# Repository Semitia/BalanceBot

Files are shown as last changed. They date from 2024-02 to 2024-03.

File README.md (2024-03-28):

## CAN负载率计算

考虑各类消息的发送端

| 单元 | FOC控制板 | TOF  | ICM  | RDK-FOC | ARM  |
| :---: | :---: | :--: | :--: | :-----: | :--: |
| 数据长度/byte | 8 |  2 | 6x2  | 8+4 | 8x2  |
| 数据频率/kHz  | 1 | 0.5  |  1 | 1 | 0.05 |

***说明：**其中TOF、ICM、机械臂均通过另加一个STM32F1来控制，STM32也挂载在CAN总线上*

一帧can消息的bit数为 $ 44 + 8*len_{data}$ ，由此可以考虑如下分配方案

### CAN1

- **FOC控制板x4：**4个关节电机——0x101~0x104
- **RDK-FOC-1：** 只控制四个电机，需8字节数据——0x100

**负载率**
$$
\kappa = \frac{108 \times 5 \times 10^3}{10^6} \times 100\% = 54\%
$$

### CAN2

- **FOC控制板x2：** 2个轮毂电机——0x105~0x106
- **RDK-FOC-1：** 只控制两个电机，需4字节数据——0x200
- **ARM：** 上位机给出的只是目标姿态，进一步由stm32控制，无需较高频率——0x301~0x302

- **TOF：** 0x310
- **ICM：** 0x320

**负载率**
$$
\kappa = \frac{(108 \times 2 + 76 + 206 \times 0.05 + 60 \times0.5 + 92\times2)\times 10^3}{10^6} \times 100\% = 51.63\%
$$

## FOC驱动板通信协议

> 下文直接引用自原开源项目作者所撰写文档

### CAN通信协议

CAN通信使用标准帧，波特率为1Mbps

**驱动反馈数据帧格式**：

不同ID的驱动板会使用不同的CAN数据帧标识符(StdID)发送反馈数据：

| 驱动ID |  StdID  | 帧类型 | DLC  |
| :----: | :-----: | :----: | :--: |
| N | 0x100+N | 标准帧 |  8 |

| DATA[0-3] |  DATA[4-5]  | DATA[6-7] |
| :---: | :---: | :---: |
| 累计转角*1000 | 当前转速*10 | 保留 |
| 单位rad |  单位rad/s  | / |
| int32_t | int16_t | / |

**驱动板接收电压指令数据帧格式**：

为节省总线带宽，不同ID的驱动板不会使用完全不同的数据帧接收数据，而是共用一个数据帧中的不同字节

共用接收数据帧 **StdID = 0x100** 的四个驱动ID为1-4：

| DATA[0-1] | DATA[2-3] | DATA[4-5] | DATA[6-7] |
| :---: | :---: | :---: | :---: |
| ID=1 输出电压 | ID=2 输出电压 | ID=3 输出电压 | ID=4 输出电压 |
| 单位mV | 单位mV | 单位mV | 单位mV |
| int16_t | int16_t | int16_t | int16_t |

共用接收数据帧 **StdID = 0x200** 的四个驱动ID为5-8：

| DATA[0-1] | DATA[2-3] | DATA[4-5] | DATA[6-7] |
| :---: | :---: | :---: | :---: |
| ID=5 输出电压 | ID=6 输出电压 | ID=7 输出电压 | ID=8 输出电压 |
| 单位mV | 单位mV | 单位mV | 单位mV |
| int16_t | int16_t | int16_t | int16_t |

也就是说，如果向总线发送StdID=0x100的数据帧，那么ID为1-4的驱动板会同时接收到指令；如果发送StdID=0x200的数据帧，则ID为5-8的驱动板会收到指令

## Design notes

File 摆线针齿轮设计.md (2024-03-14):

[机械臂驱动器 ——摆线减速器参数设计和组装测试 - 知乎 (zhihu.com)](https://zhuanlan.zhihu.com/p/652012423)

#### 取减速比 Za = 10

| | 3510无刷电机 | 3510+减速器 | 宇树A1 |
| --- | --- | --- | --- |
| 额定扭矩/NM | 0.11 | | |
| 峰值扭矩/NM | 0.16 | | 33.5 |
| 最大转速/rad/s | 130 | | 21 |
| 额定转速/rad/s | 98 | | |
| 质量/g | 73 | | 605 |
| 电压/V | 12 | | 20~40  |
| 额定电流/A | 0.53 | | |
| 堵转电流/A | 0.8 | | |
| 极对数 | 11 | | |

#### 针轮中心圆直径 

$D_p := $ 36mm

#### 偏心距 

a := 0.7mm
$$
K_1 := 0.42 \\
Z_b = Z_a + 1 = 11 \\
R_p = \frac{D_p}{2} = 18mm \\
a = \frac{K_1 R_p}{Z_b} = 0.687mm
$$

#### 针齿销直径

$d_{rp}$  := 3.5mm 
$$
K_2 = 2.9 \\
d_{rp} = \frac{D_p \sin{\frac{\pi}{Z_b}}}{K_2} = 3.38mm
$$

#### 摆线轮

中心孔直径 $D_1 := 15mm$

齿根圆直径$D_{fc} = D_p - 2a - d_{rp} = 31.1mm$

齿顶圆直径$D_{ac} = D_p + 2a - d_{rp} = 33.9mm$

盘厚 3mm

柱销中心圆直径 $D_w = \frac{D_{fc} + D_1}{2} = 23.05mm$ 

#### 柱销

取柱销直径 $d_{sw}(=d_{rw})$ = 3.5mm

柱销孔直径 $d_w = d_{rw} + 2a = 5.9mm$

然而经过实际测试，按照公式计算出的偏心距较小，对加工精度要求较高，工作起来较为困难。故适当增加偏心距重新设计减速器。

a=1.2mm

齿根圆直径$D_{fc} = D_p - 2a - d_{rp} = 30.1mm$

齿顶圆直径$D_{ac} = D_p + 2a - d_{rp} = 34.9mm$

柱销中心圆直径 $D_w = \frac{D_{fc} + D_1}{2} = 22.55mm$ 

柱销孔直径 $d_w = d_{rw} + 2a = 5.9mm$

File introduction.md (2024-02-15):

## 硬件

### 电机选型

[【干货】你必须要知道的无人机/航模基础知识---无刷电机 (zhihu.com)](https://www.zhihu.com/tardis/zm/art/139795659?source_id=1005)

[高端国产云台电机GB3505直流无刷电机可配单独AS5048A编码器马达-淘宝网 (taobao.com)](https://item.taobao.com/item.htm?id=639218649915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)



[手持相机自拍杆 微型航模云台电机 2804 钕铁硼强磁 三相无刷电机-淘宝网 (taobao.com)](https://item.taobao.com/item.htm?spm=a230r.1.14.33.890744afRuM5Ug&id=718309339502&ns=1&abbucket=8#detail)

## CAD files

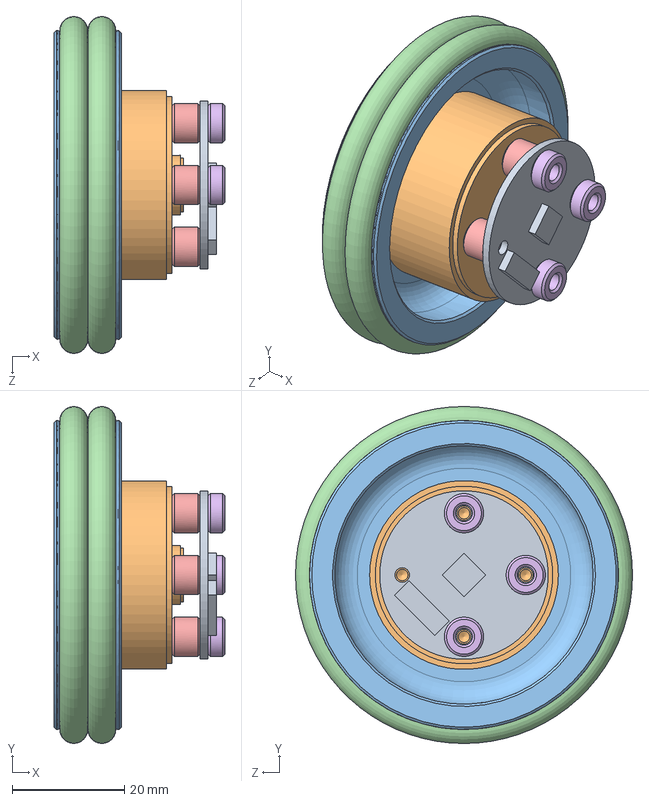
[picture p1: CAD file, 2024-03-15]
SW/轮毂电机/轮部2804.SLDASM
30.4 x 60.0 x 60.0 mm
驱动板
2804电机
橡胶圈轮子
橡胶圈 x 2
驱动板垫脚 x 4
驱动板垫脚3mm x 3

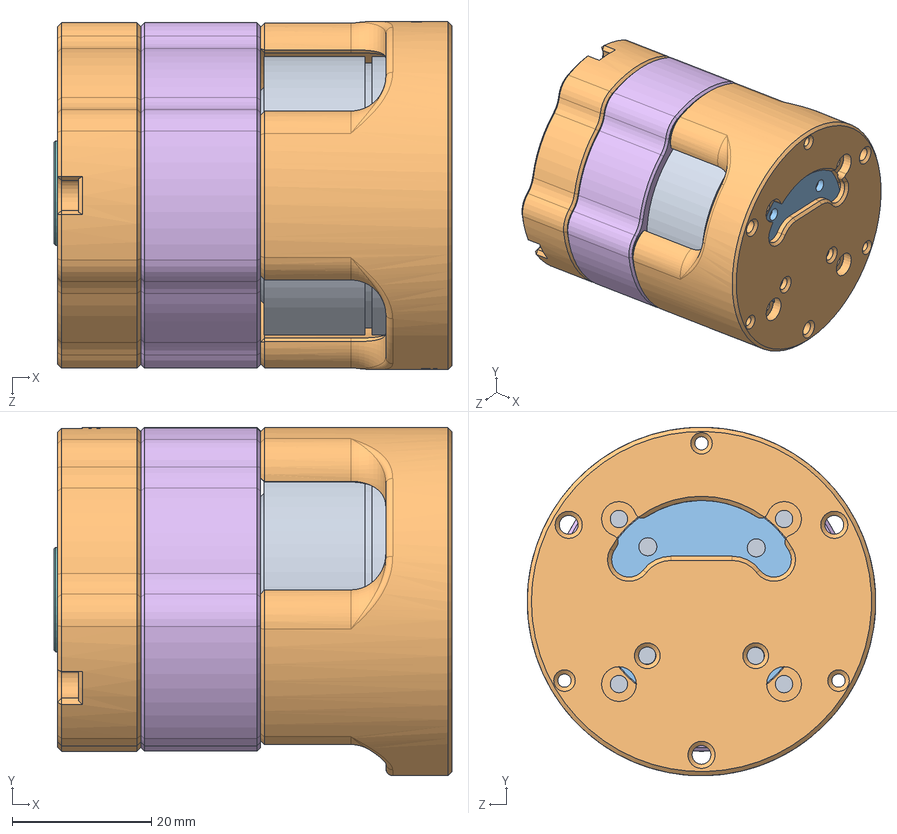
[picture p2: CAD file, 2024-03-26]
SW/关节电机/3510减速电机.SLDASM
57.1 x 50.0 x 50.0 mm
减速箱基座
输入轴
10x15x4 x 3
W机构底盖
针齿座
M3.5x14
W机构输出轴
15x24x5
端盖
驱动板
偏心轮 x 2
摆线轮1.2 x 2
M3_5x16

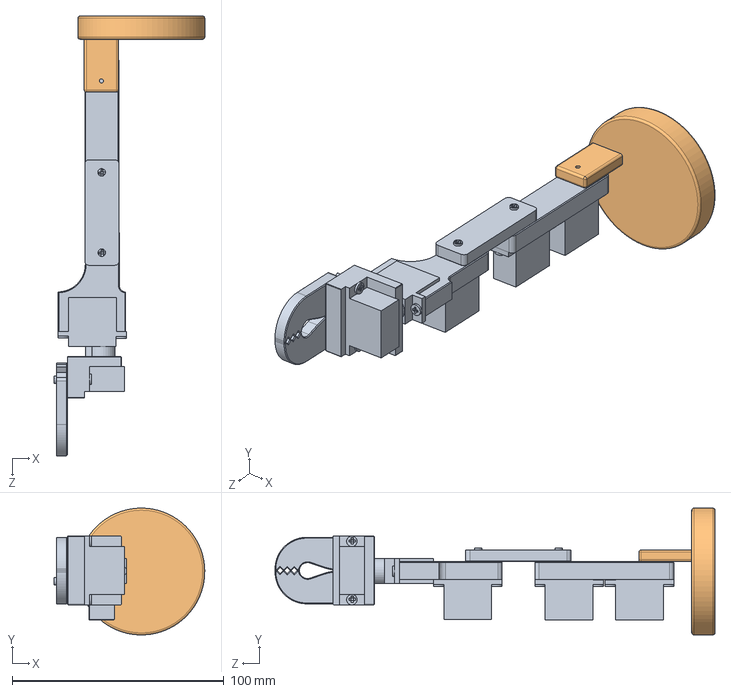
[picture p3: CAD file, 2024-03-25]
SW/机械臂/机械臂.SLDASM
71.2 x 60.0 x 208.0 mm
arm.stp
底座

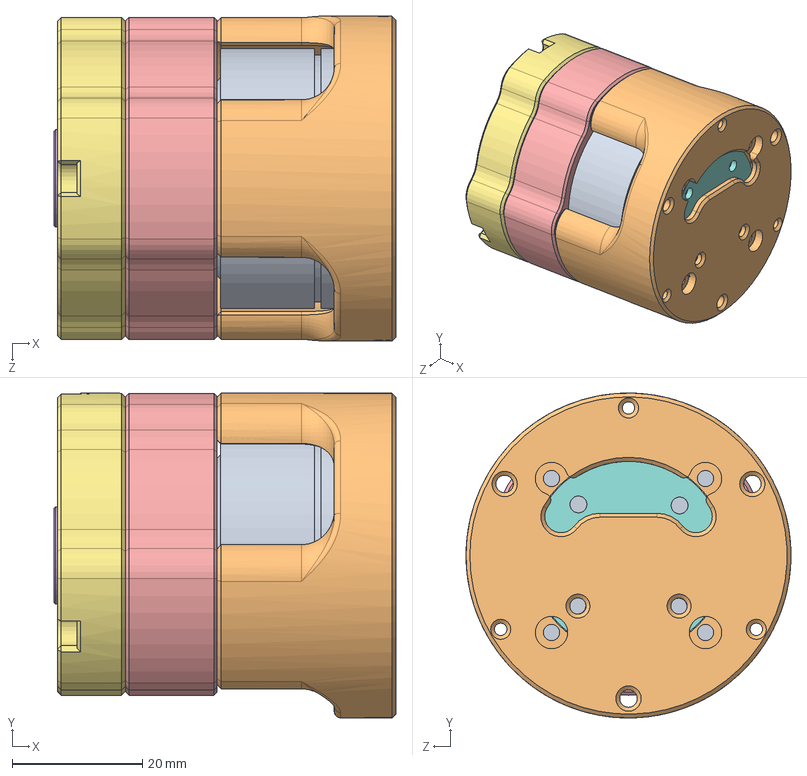
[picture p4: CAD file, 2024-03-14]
SW/关节电机/3510减速电机_单摆.SLDASM
52.6 x 50.0 x 50.0 mm
减速箱基座
输入轴
10x15x4 x 2
M3.5x14
15x24x5
端盖
驱动板
偏心轮
摆线轮1.2
W机构底盖_单摆
M4x12
针齿座_单摆
W机构输出轴_单摆

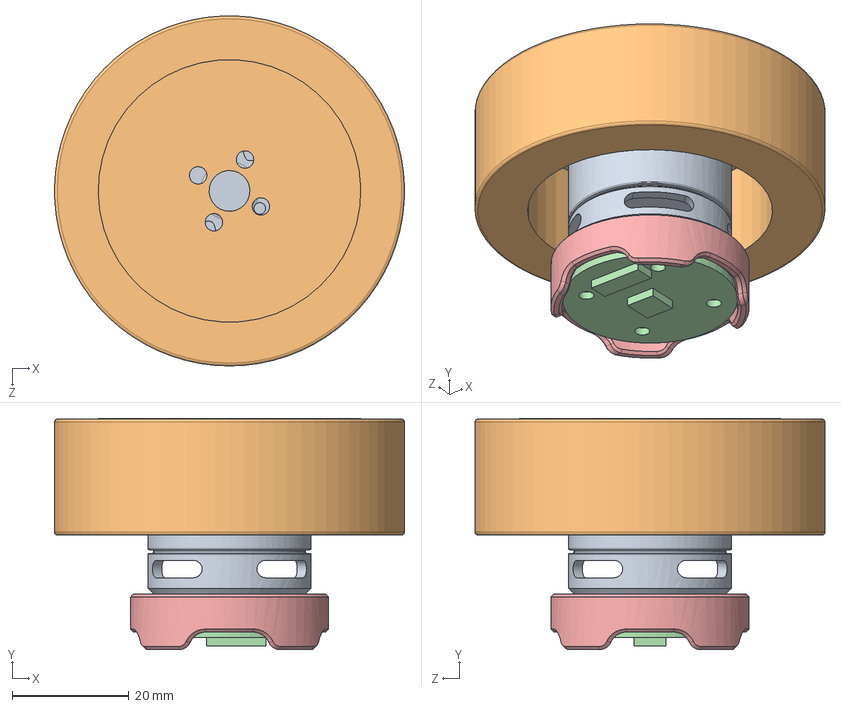
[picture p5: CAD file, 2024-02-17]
SW/轮毂电机/轮部.SLDASM
60.0 x 39.6 x 60.0 mm
轮子
联轴器
驱动板
2208后盖

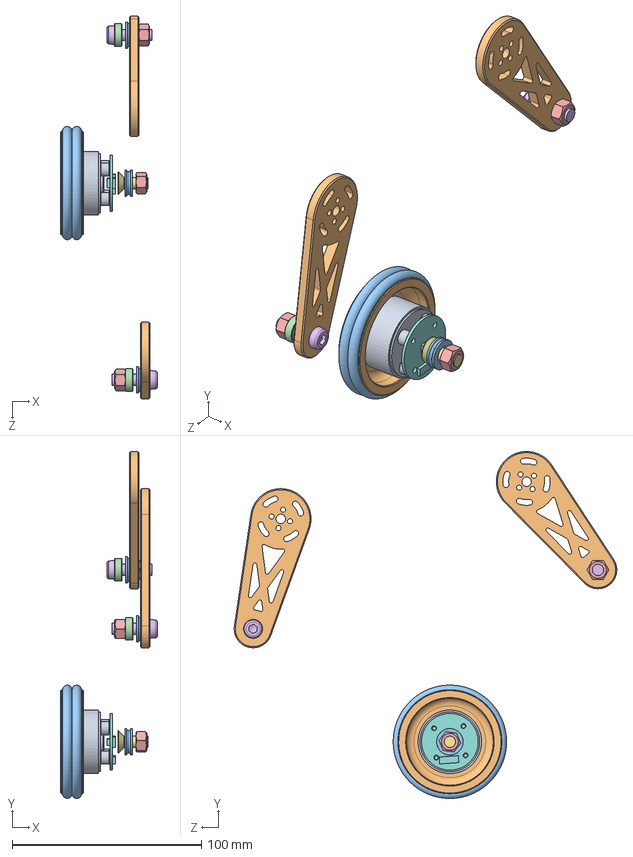
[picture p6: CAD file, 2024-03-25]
SW/腿.SLDASM
51.1 x 183.5 x 202.4 mm
大腿 x 2
推力轴承 x 3
6x12x4 x 2
hex nuts, style 2-grades ab gb x 3
hex lobular socket head cap screws-4.8 gb x 2
hex lobular socket ctsk screws gb
驱动板
2804电机
橡胶圈轮子
橡胶圈 x 2
驱动板垫脚 x 4

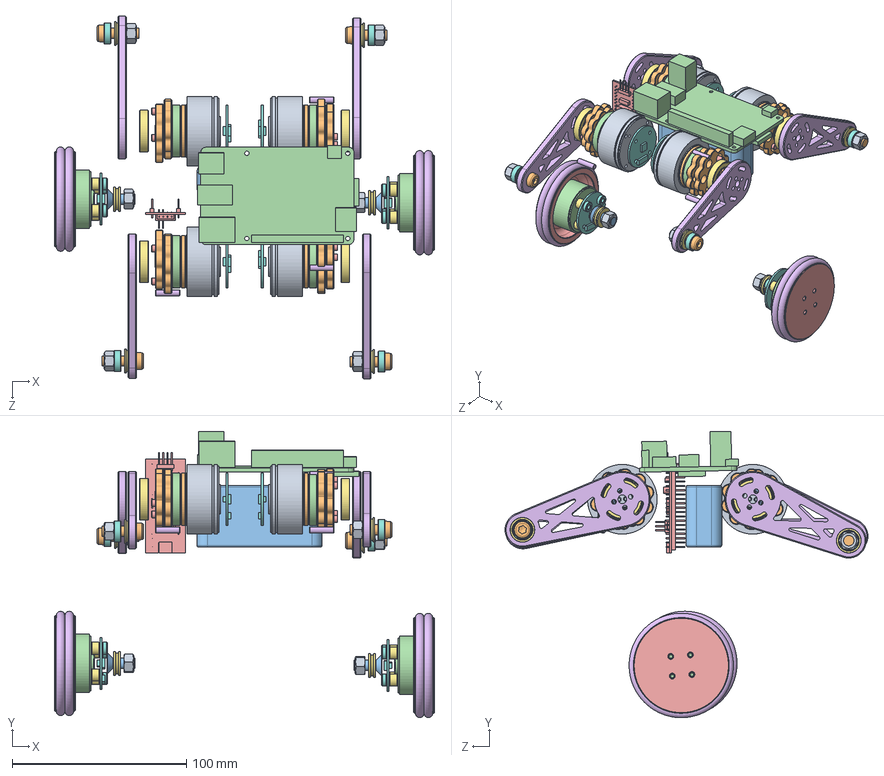
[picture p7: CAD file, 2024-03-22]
SW/BalanceBot_2804.SLDASM
218.3 x 164.5 x 208.5 mm
输入轴 x 4
10x15x4 x 12
W机构底盖 x 4
M4x14 x 8
M3.5x14 x 4
15x24x5 x 4
驱动板 x 6
偏心轮 x 8
摆线轮1.2 x 8
电池
RDKx3
stm32f103c8t6-board
大腿 x 4
推力轴承 x 6
6x12x4 x 4
hex nuts, style 2-grades ab gb x 6
hex lobular socket head cap screws-4.8 gb x 4
hex lobular socket ctsk screws gb x 2
2804电机 x 2
橡胶圈轮子 x 2
橡胶圈 x 4
驱动板垫脚 x 8
驱动板垫脚3mm x 6

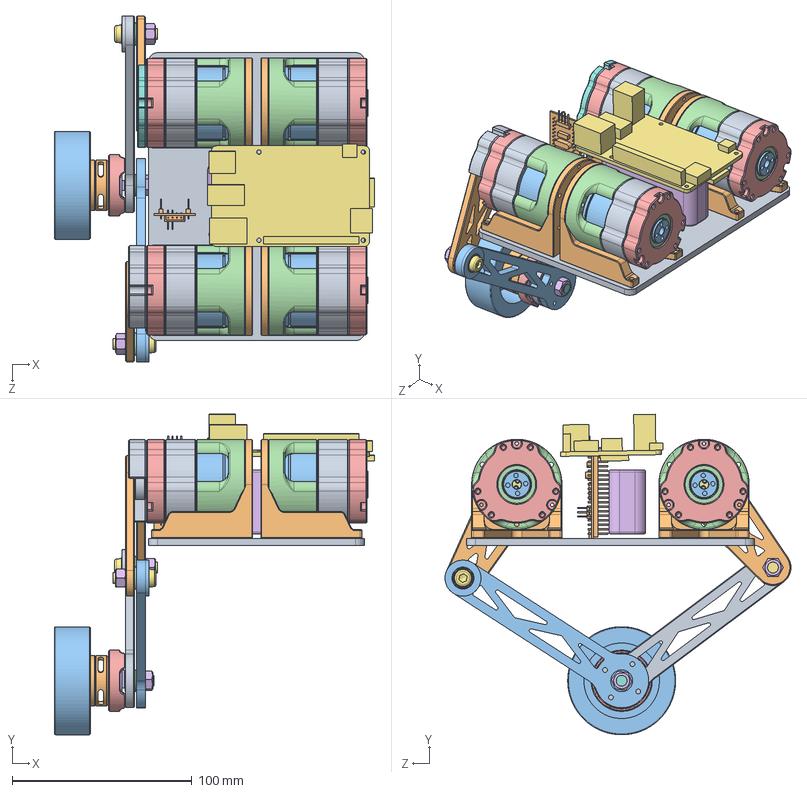
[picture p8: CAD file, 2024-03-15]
SW/BalanceBot.SLDASM
178.0 x 178.1 x 192.2 mm
底板
关节电机支架 x 4
减速箱基座 x 4
输入轴 x 4
10x15x4 x 12
W机构底盖 x 4
M4x14 x 8
针齿座 x 4
M3.5x14 x 4
W机构输出轴 x 4
15x24x5 x 4
端盖 x 4
驱动板 x 5
偏心轮 x 8
摆线轮1.2 x 8
大腿垫高
大腿 x 2
小腿
推力轴承 x 3
6x12x4 x 2
hex nuts, style 2-grades ab gb x 3
hex lobular socket head cap screws-4.8 gb x 2
hex lobular socket ctsk screws gb
小腿沉头
轮子
联轴器
2208后盖
电池
RDKx3
限位圈
限位圈加高
stm32f103c8t6-board

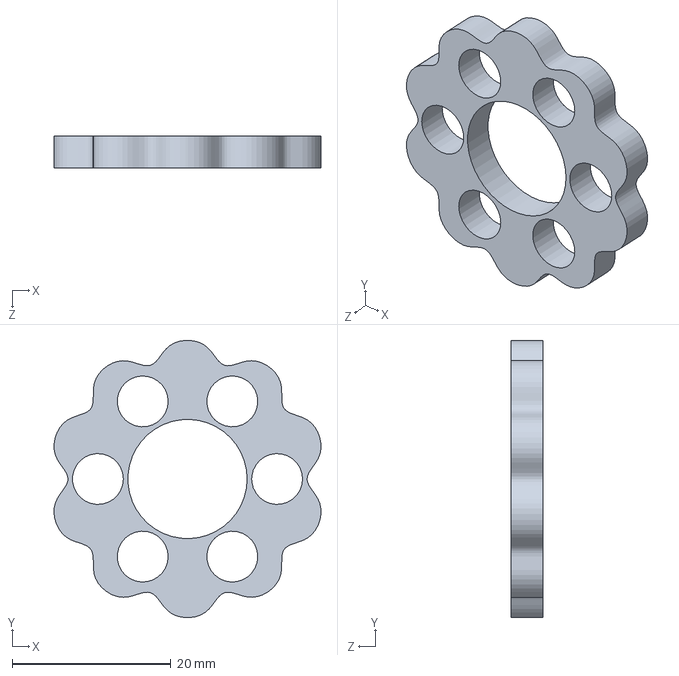
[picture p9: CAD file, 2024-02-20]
SW/关节电机/step/zjgc.SLDASM
33.6 x 34.9 x 4.00 mm

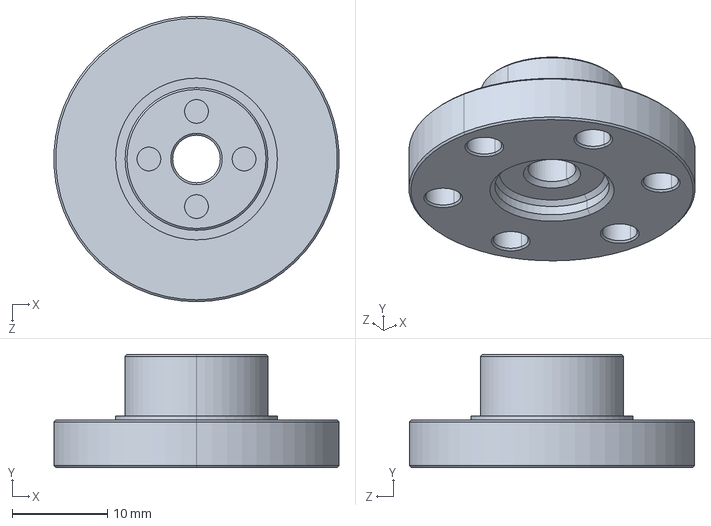
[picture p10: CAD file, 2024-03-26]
SW/关节电机/step/W机构输出轴.STEP
30.0 x 11.9 x 30.0 mm

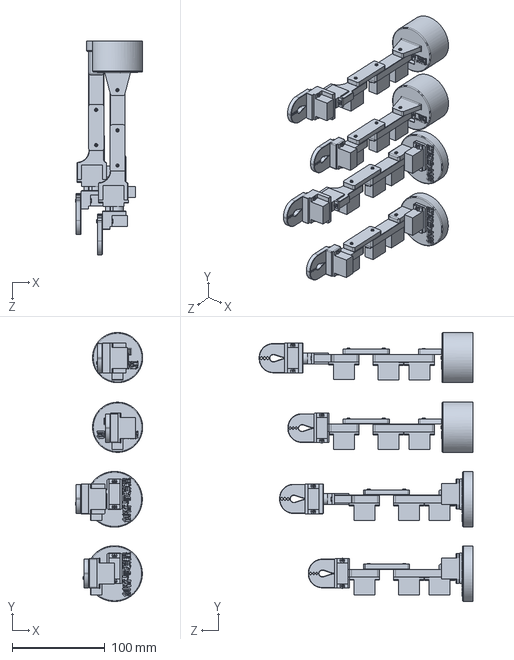
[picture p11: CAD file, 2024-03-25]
SW/机械臂/raw_arm.stp.SLDPRT
72.5 x 289.5 x 230.0 mm

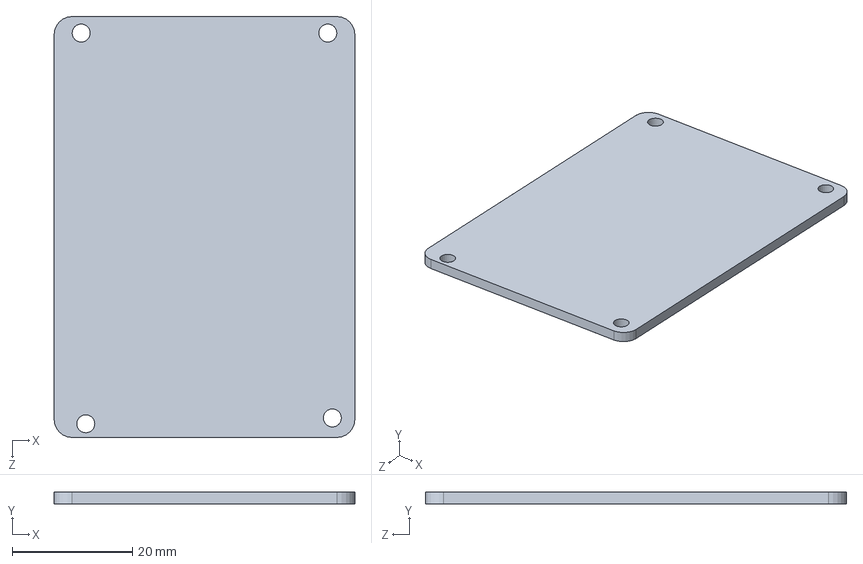
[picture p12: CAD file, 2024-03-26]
SW/洞洞板.SLDPRT
50.0 x 2.00 x 70.0 mm

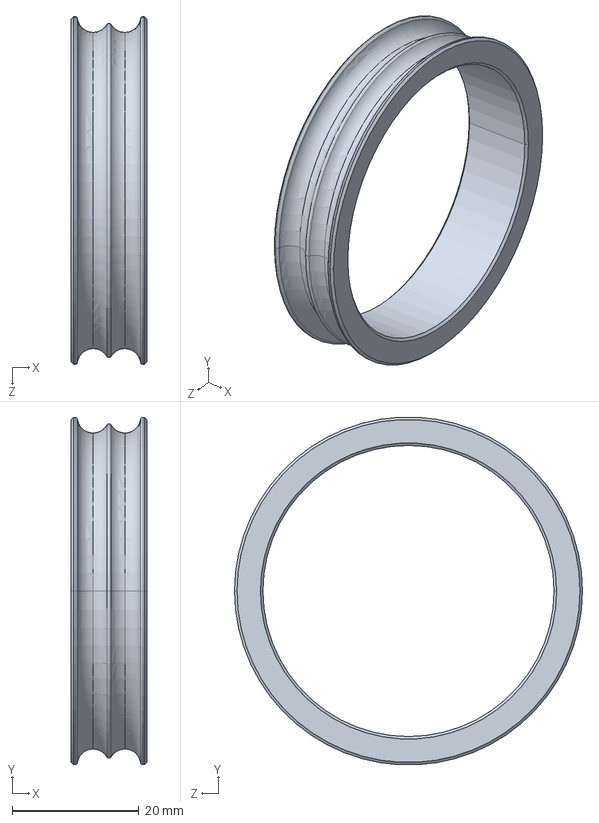
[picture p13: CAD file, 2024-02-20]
SW/轮毂电机/step/橡胶圈轮子.STEP
12.0 x 54.9 x 55.0 mm

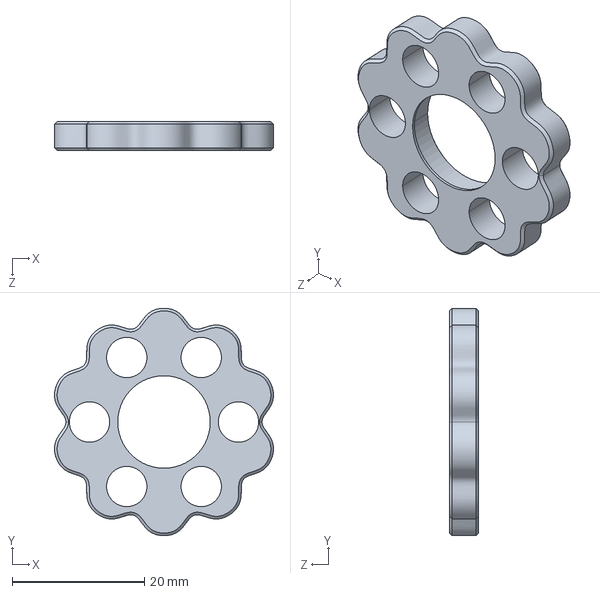
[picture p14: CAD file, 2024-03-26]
SW/关节电机/step/摆线轮1.2_297.STEP
33.2 x 34.4 x 4.40 mm

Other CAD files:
SW/机械臂/底座.SLDPRT
SW/机械臂底座.SLDPRT
SW/轮毂电机/step/橡胶圈轮子(单圈).STEP
SW/轮毂电机/驱动板垫脚.SLDPRT
SW/6x12x4.SLDPRT
SW/RDKx3.SLDPRT
SW/arm.stp.SLDPRT
SW/stm32f103c8t6-board.SLDPRT
SW/上板.SLDPRT
SW/关节电机/10x15x4.SLDPRT
SW/关节电机/15x24x5.SLDPRT
SW/关节电机/3510.SLDPRT
SW/关节电机/M3.5x14.SLDPRT
SW/关节电机/M3_5x16.SLDPRT
SW/关节电机/M4x12.SLDPRT
SW/关节电机/M4x14.SLDPRT
SW/关节电机/W机构底盖.SLDPRT
SW/关节电机/W机构底盖_单摆.SLDPRT
SW/关节电机/W机构输出轴.SLDPRT
SW/关节电机/W机构输出轴_单摆.SLDPRT
SW/关节电机/cycloid.step
SW/关节电机/step/M3.5x14.STEP
SW/关节电机/step/M4x14.STEP
SW/关节电机/step/W机构底盖.STEP
SW/关节电机/step/zjgc.DXF
SW/关节电机/step/偏心轮(无轴承).STEP
SW/关节电机/step/偏心轮.STEP
SW/关节电机/step/减速箱基座(打印测试）.STEP
SW/关节电机/step/减速箱基座.STEP
SW/关节电机/step/加工.3mf
SW/关节电机/step/摆线轮.STEP
SW/关节电机/step/摆线轮0.99x2.STEP
SW/关节电机/step/摆线轮1.2.STEP
SW/关节电机/step/摆线轮1.2_298.STEP
SW/关节电机/step/摆线轮1.2_2985.STEP
SW/关节电机/step/摆线轮1.2_299.STEP
SW/关节电机/step/摆线轮1.2_30.1mm.STEP
SW/关节电机/step/摆线轮1.2_30_6.1mm.STEP
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

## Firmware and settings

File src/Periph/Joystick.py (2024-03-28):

import pygame


class JoystickCtrl:
    def __init__(self):
        # 初始化pygame和joystick模块
        pygame.init()
        pygame.joystick.init()
        # 检查是否有手柄连接
        self.joystick_count = pygame.joystick.get_count()
        if self.joystick_count == 0:
            raise OSError('No joysticks detected')
        # 初始化第一个手柄
        self.joystick = pygame.joystick.Joystick(0)
        self.joystick.init()

    def read_input(self):
        # 更新事件队列，这一步是必须的
        pygame.event.pump()
        # 读取手柄的轴和按钮状态
        axes = [self.joystick.get_axis(i) for i in range(self.joystick.get_numaxes())]
        buttons = [self.joystick.get_button(i) for i in range(self.joystick.get_numbuttons())]
        return axes, buttons

    def close(self):
        # 在程序结束时关闭手柄
        if self.joystick:
            self.joystick.quit()
        pygame.joystick.quit()
        pygame.quit()


if __name__ == '__main__':
    # 示例使用
    controller = JoystickCtrl()
    while True:
        ex_axes, ex_buttons = controller.read_input()
        print(f"Axes: {ex_axes}")
        print(f"Buttons: {ex_buttons}")
        # 这里可以加上一段延时来限制读取的频率，例如 pygame.time.wait(100)

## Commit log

2024-02-15 3510 电机与摆线针减速器
    [10x15x4.SLDPRT, 15x24x5.SLDPRT, 3510.SLDPRT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]
2024-02-15 关节电机支架
    [3510减速电机.SLDASM, BalanceBot.SLDASM, 关节电机支架.SLDPRT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]
2024-02-17 限位和负载
    [3510减速电机.SLDASM, BalanceBot.SLDASM, M3.5x14.STEP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]
2024-02-18 公差测试与尺寸修改
    [3510减速电机.SLDASM, W机构底盖.SLDPRT, W机构底盖.STEP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]
2024-02-19 new cycloid
    [cycloid.step]
2024-02-20 尺寸细节
    [3510减速电机.SLDASM, BalanceBot.SLDASM, W机构底盖.SLDPRT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]
2024-02-20 增加外摆线轮与针齿接触面积
    [3510减速电机.SLDASM, W机构底盖.SLDPRT, W机构底盖.STEP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]
2024-02-21 尺寸微调
    [3510减速电机.SLDASM, BalanceBot.SLDASM, 偏心轮.SLDPRT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]
2024-03-14 轴隙调整
    [3510减速电机.SLDASM, W机构底盖.SLDPRT, 偏心轮.SLDPRT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]
2024-03-14 增加单摆
    [3510减速电机.SLDASM, 3510减速电机_单摆.SLDASM, M4x12.SLDPRT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]
2024-03-14 柱销改3.5
    [3510减速电机.SLDASM, W机构底盖.SLDPRT, W机构底盖.STEP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]
2024-03-22 重新装配腿
    [3510减速电机.SLDASM, BalanceBot_2804.SLDASM, 小腿.SLDPRT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]
2024-03-26 开始虚空写代码
    [3510减速电机.SLDASM, M3_5x16.SLDPRT, W机构底盖.SLDPRT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]
2024-03-27 QT实现的示波器
2024-03-27 添加电机类
2024-03-28 do_mpc不好用，换自己写
2024-03-29 MPC库
2024-03-30 很捞的非线性mpc
2024-04-15 电路板安装
2024-04-19 电机能转，通讯能通
2024-04-22 模型修改
